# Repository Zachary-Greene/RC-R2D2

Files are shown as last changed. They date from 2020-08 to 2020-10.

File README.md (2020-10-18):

# Mini Remote Control R2D2

This repo is for my mini remote control R2D2 project. It includes all the stl files, all the code files, and the f3z (Fusion 360) file. It also includes some Fusion 360 renders and some extra images.

## Prerequisites
All you need is access to a 3D printer, some skills with through-hole soldering and the parts needed.

## Assembly
First solder the components on to the PCB, making sure that they are the right way around and aligned with the silkscreen. Then place the main PCB in the bottom of the body. Place the motors in the mounts in the feet and push the wires through the feet and legs. Then push and glue if necessary the foot to the corresponding leg, eg left foot to left leg. Then push the legs through the holes in the body, making sure to get the in the right orientation, then push the fastening bolt through the holes to secure the legs in the correct position, then glue them. Repeat for the other leg. For the center foot, put the axle through the wheel and glue the axle in place, not the wheel. For the head mechanism, put the motor inside the head stem with the motor lock glued in place under it, then slide the head stem on to the pegs pointing upwards from the body, from there, put the head on to the head stem with some glue. You then plug the wires into the main PCB, turn it on and put the head on top. For the controller, solder the components on and enjoy. (The wheels are lego wheels as they are what I have handy from siblings and will probably be changed in the coming time.)

## Programming
Plug the ATmega328P into a programmer and burn the bootloader if it doesnt already have one. Then upload the corresponding sketch and put the IC in the proper socket.

## Parts
### Main PCB
* ATmega328P Digikey x1
* LD1117V33 (COM-00526) Sparkfun/Core Electronics x1
* NRF24L01 x1
* NPN Transistor (COM-00521) Sparkfun/Core Electronics x12
* 4xAA Battery Holder (PRT-12083) Sparkfun/Core Electronics x1
#### The following is for an optional speaker system
* 0.1uF Ceramic Capacitor (COM-08375) Sparkfun/Core Electronics x1
* 1.25K Ohm Resistor Digikey x1
* 8 Ohm Speaker x1
* DFPlayer Mini (DFR0299) Core Electronics x1

### Controller PCB
* ATmega328P Digikey x1
* LD1117V33 (COM-00526) Sparkfun/Core Electronics x1
* Thumb Joystick (COM-09032) Sparkfun/Core Electronics x2
* NRF24L01 x1
* 4xAA Battery Holder (PRT-12083) Sparkfun/Core Electronics x1

## Renders
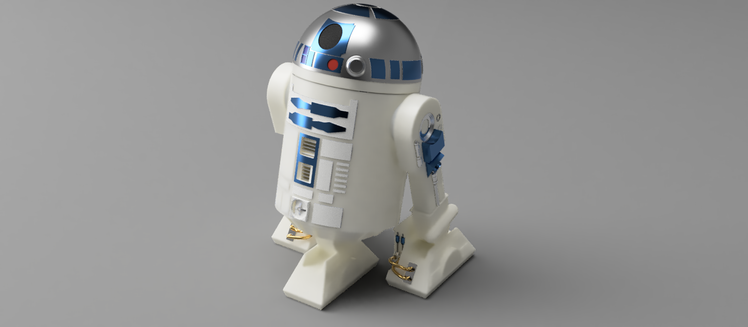
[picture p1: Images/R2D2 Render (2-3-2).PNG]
R2D2 2-3-2 Configuration

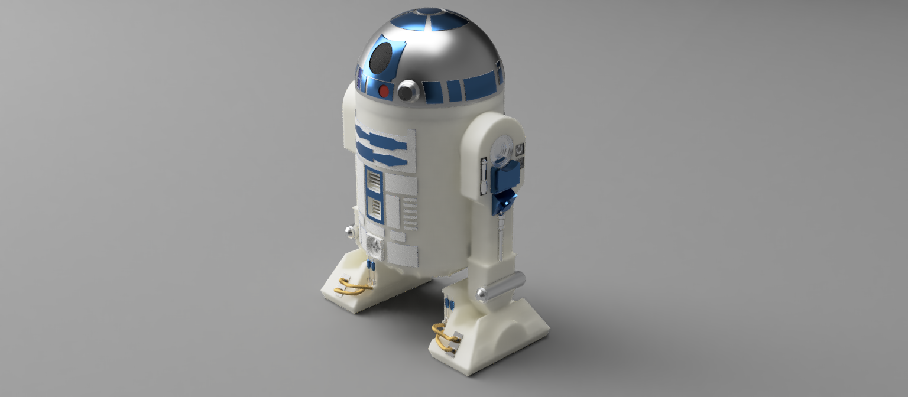
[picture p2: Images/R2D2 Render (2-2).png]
R2D2 2-2 Configuration


## License
See LICENSE.md

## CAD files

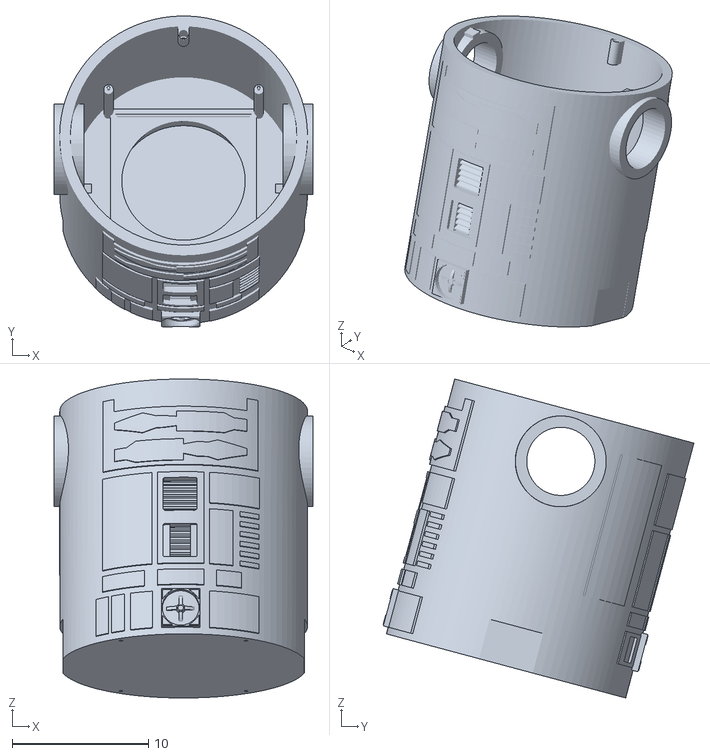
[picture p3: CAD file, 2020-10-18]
STL/Body/Body.stl
19.0 x 22.8 x 23.4

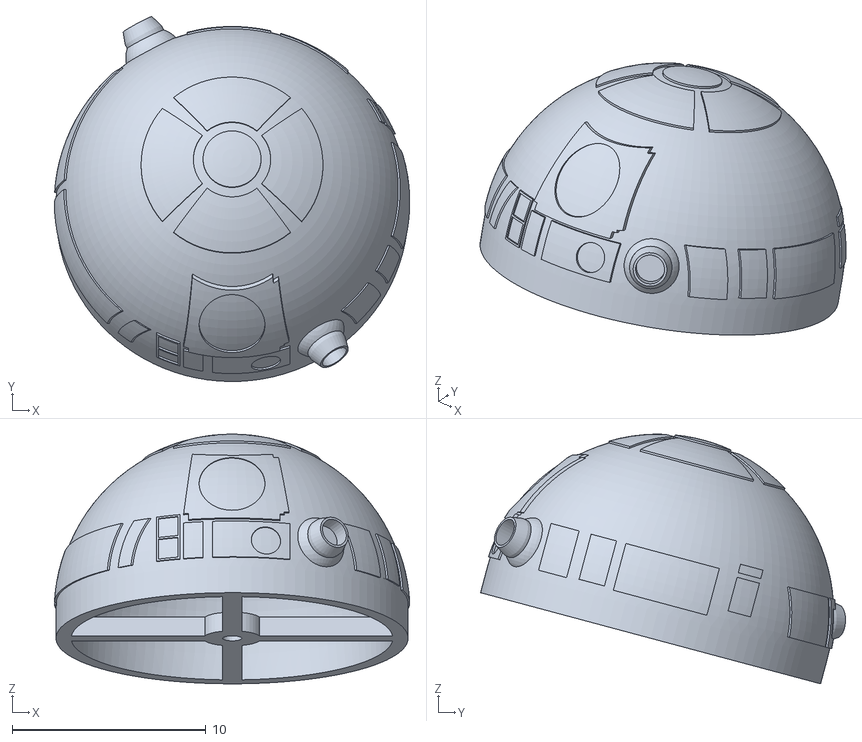
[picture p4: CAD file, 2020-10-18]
STL/Head/Head.stl
18.4 x 18.9 x 12.9

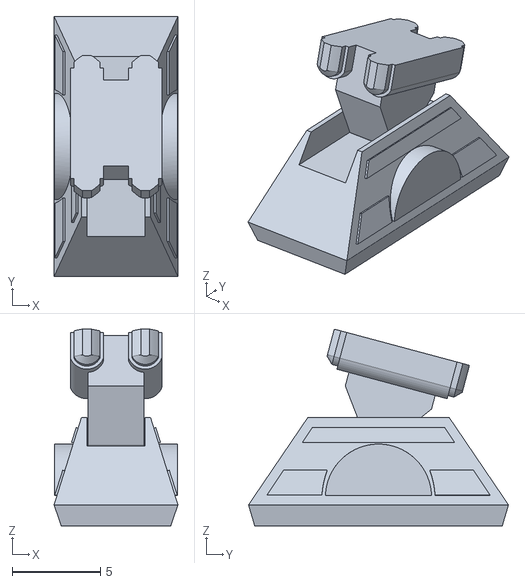
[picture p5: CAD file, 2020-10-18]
STL/Legs/Centre Foot.stl
7.01 x 14.7 x 11.1

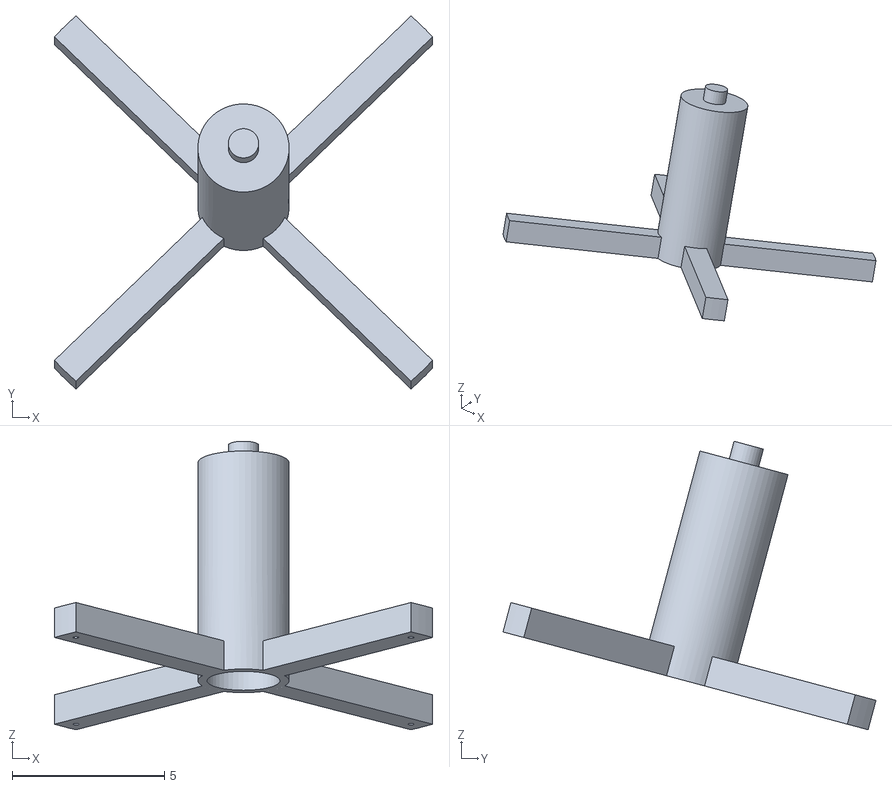
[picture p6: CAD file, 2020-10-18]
STL/Head/Head Stem.stl
12.4 x 12.3 x 9.48

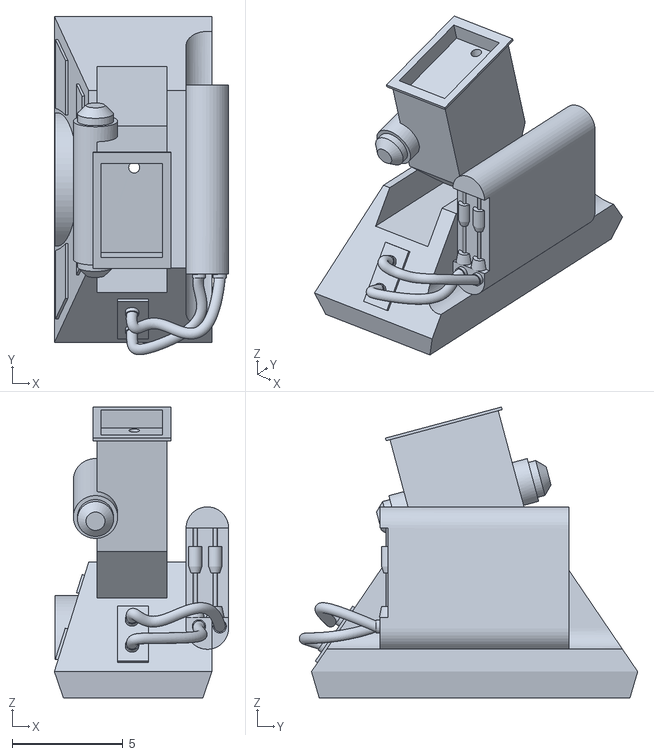
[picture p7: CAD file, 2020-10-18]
STL/Legs/Right Foot.stl
7.85 x 15.3 x 13.1

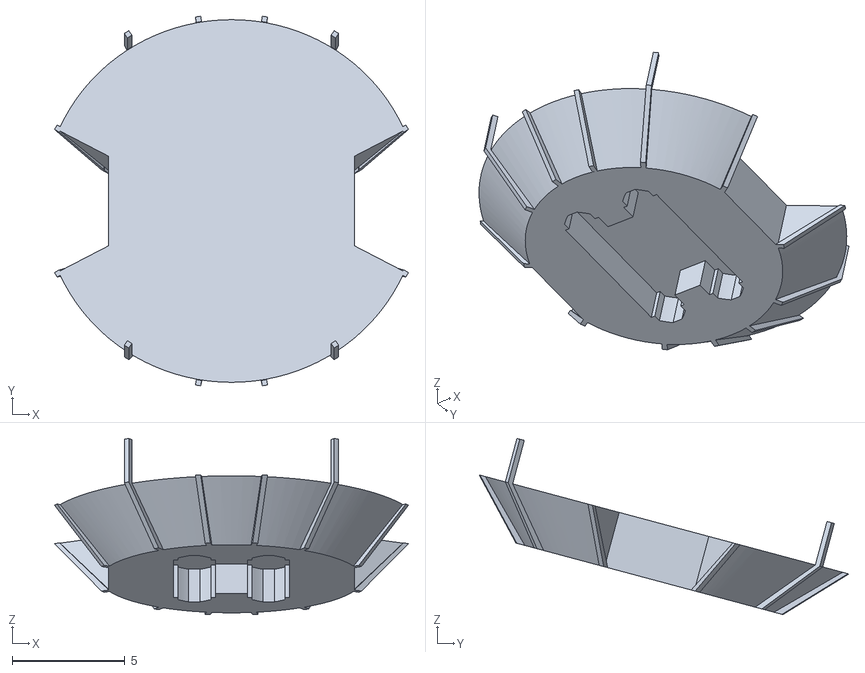
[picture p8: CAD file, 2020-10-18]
STL/Body/Skirt.stl
15.7 x 16.4 x 7.82

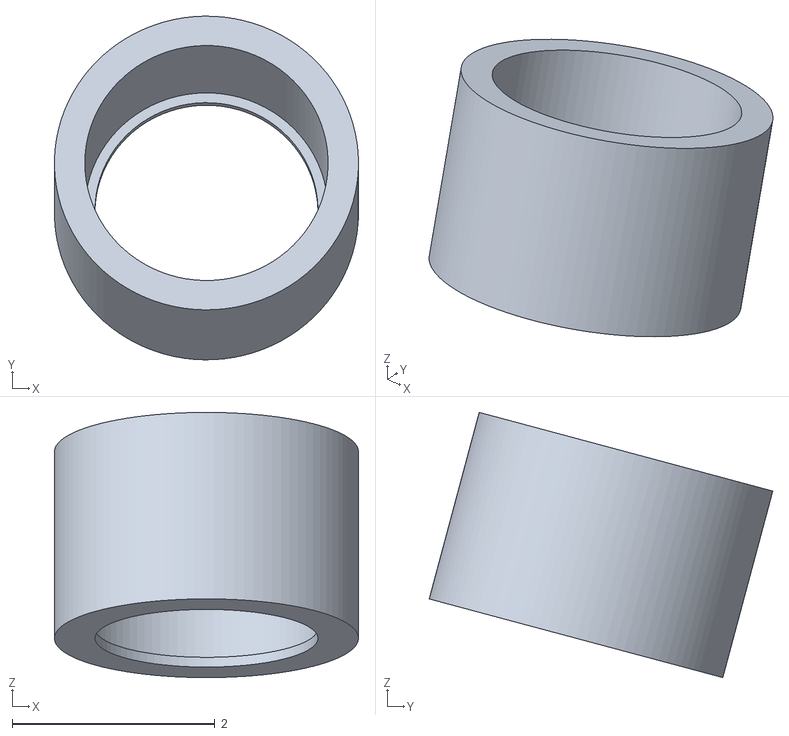
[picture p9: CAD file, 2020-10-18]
STL/Head/Motor Lock.stl
3.00 x 3.39 x 2.62

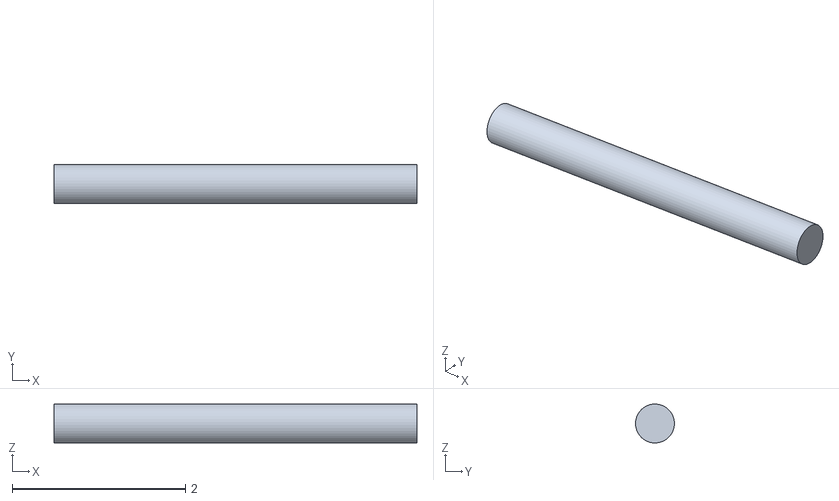
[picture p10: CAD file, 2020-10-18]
STL/Legs/Center Axle.stl
4.19 x 0.449 x 0.45

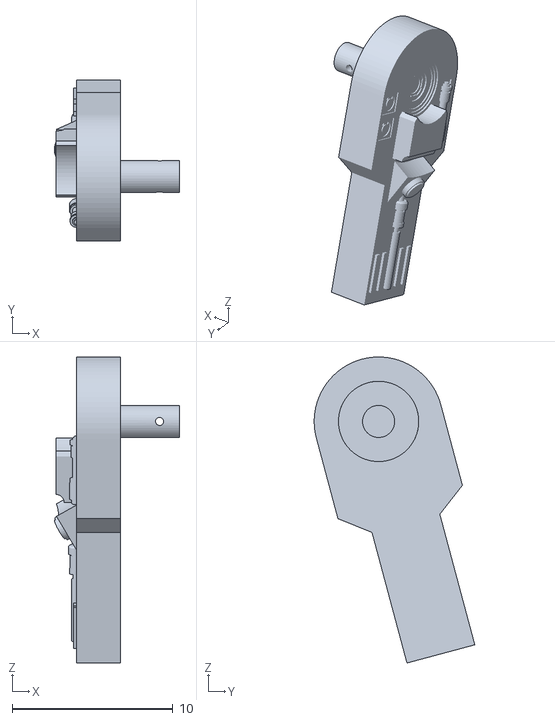
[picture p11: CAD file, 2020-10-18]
STL/Legs/Right Leg.stl
7.80 x 10.0 x 19.1

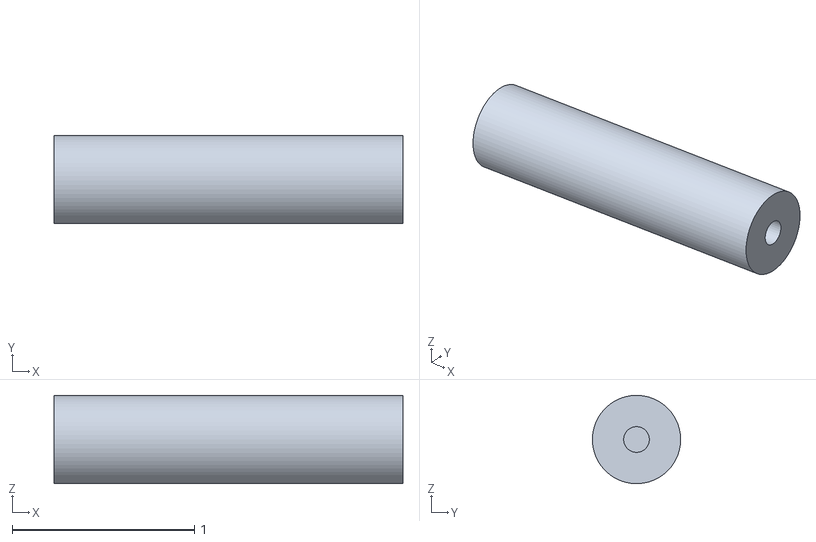
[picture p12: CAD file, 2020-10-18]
STL/Legs/Wheel Adapter (Print 2).stl
1.92 x 0.485 x 0.485

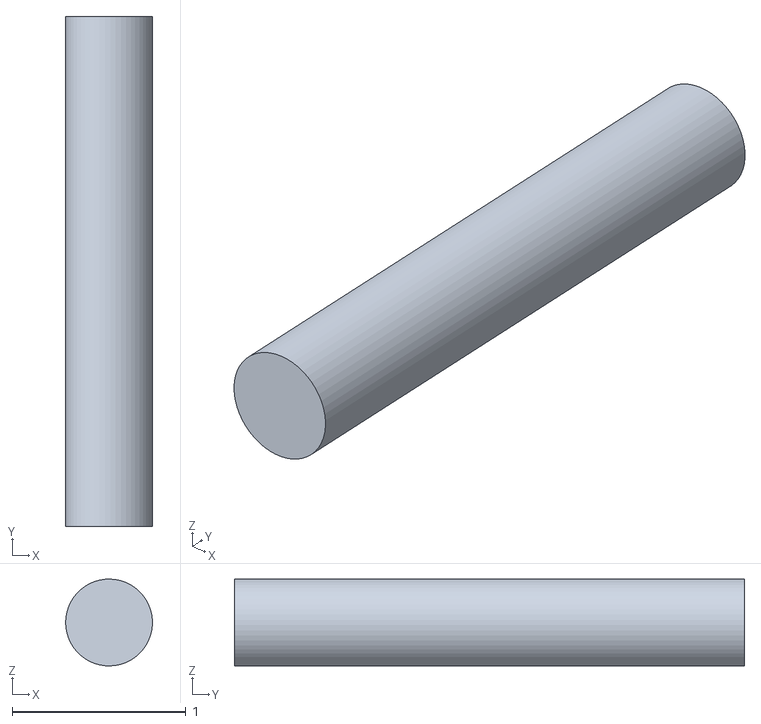
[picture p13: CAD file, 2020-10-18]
STL/Body/Fastening Bolt (Print 2).stl
0.5 x 2.93 x 0.5

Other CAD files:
STL/Legs/Left Leg.stl
STL/Legs/Left Foot.stl

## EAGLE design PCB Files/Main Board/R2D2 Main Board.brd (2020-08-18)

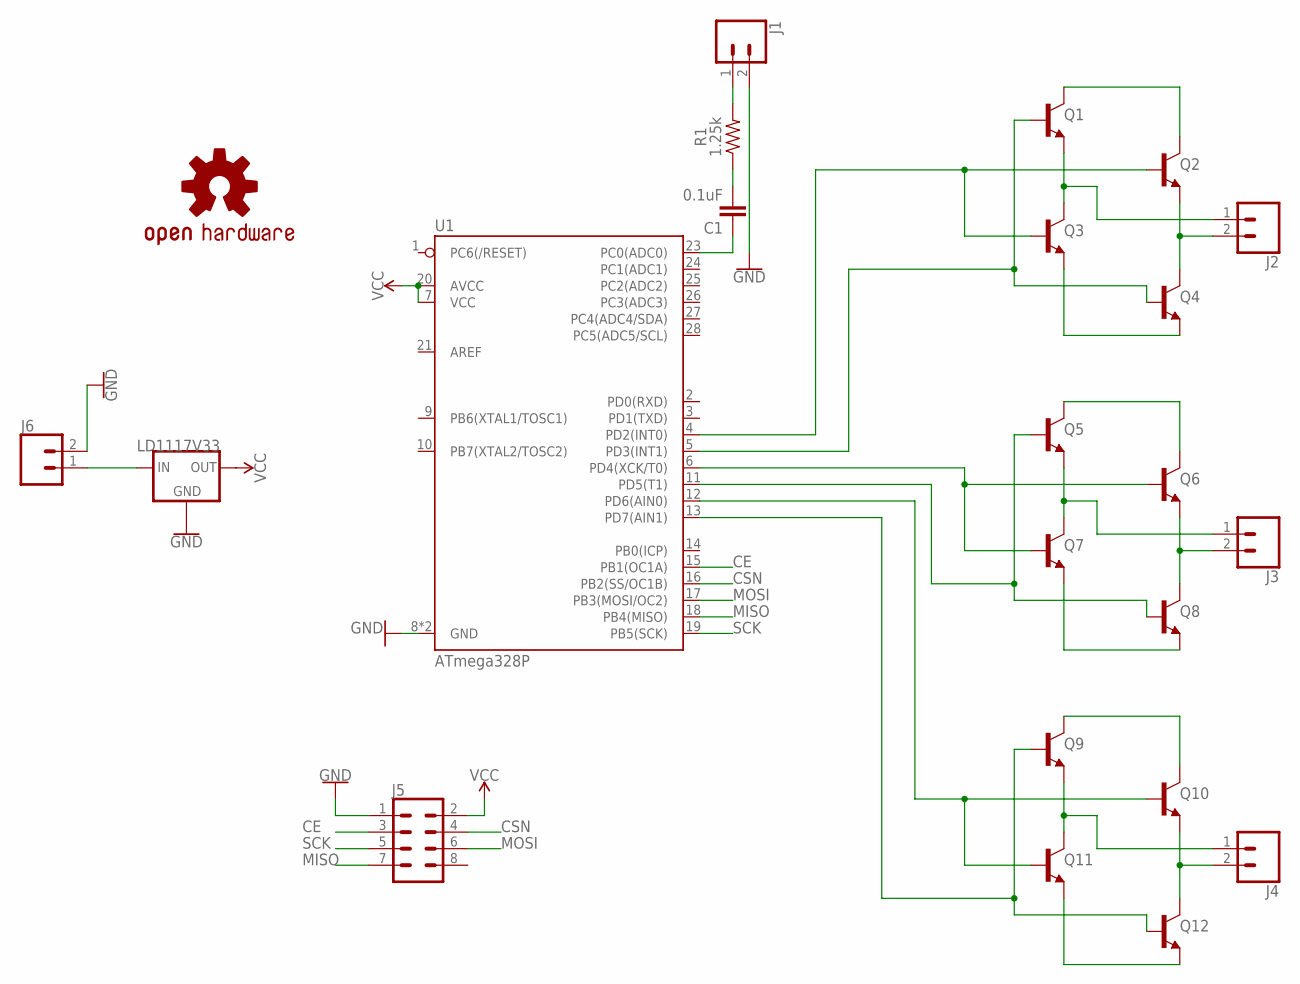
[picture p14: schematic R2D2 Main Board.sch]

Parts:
C1: 0.1uF; CAP-PTH-SMALL-KIT
J1, J2, J3, J4, J6: CONN_02; 1X02
J5: CONN_04X2; 2X4
LOGO1: OSHW-LOGOL; OSHW-LOGO-L
Q1, Q2, Q3, Q4, Q5, Q6, Q7, Q8, Q9, Q10, Q11, Q12: 200mA/40V; TO-92
R1: 1.25k; AXIAL-0.3
U1: ATmega328P; DIP28
U$1: LD1117V33; 78XXL

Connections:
CE: J5.3, U1.15 (PB1(OC1A))
CSN: J5.4, U1.16 (PB2(SS/OC1B))
GND: J1.2, J5.1, J6.2, U1.8 (GND), U1.22 (GND), U$1.IN (GND)
MISO: J5.7, U1.18 (PB4(MISO))
MOSI: J5.6, U1.17 (PB3(MOSI/OC2))
unnamed: Q1.3 (C), Q2.3 (C)
unnamed: Q3.1 (E), Q4.1 (E)
unnamed: J2.2, Q2.1 (E), Q4.3 (C)
unnamed: J2.1, Q1.1 (E), Q3.3 (C)
unnamed: Q2.2 (B), Q3.2 (B), U1.4 (PD2(INT0))
unnamed: Q1.2 (B), Q4.2 (B), U1.5 (PD3(INT1))
unnamed: Q5.3 (C), Q6.3 (C)
unnamed: Q7.1 (E), Q8.1 (E)
unnamed: J3.2, Q6.1 (E), Q8.3 (C)
unnamed: J3.1, Q5.1 (E), Q7.3 (C)
unnamed: Q6.2 (B), Q7.2 (B), U1.6 (PD4(XCK/T0))
unnamed: Q5.2 (B), Q8.2 (B), U1.11 (PD5(T1))
unnamed: Q9.3 (C), Q10.3 (C)
unnamed: Q11.1 (E), Q12.1 (E)
unnamed: J4.2, Q10.1 (E), Q12.3 (C)
unnamed: J4.1, Q9.1 (E), Q11.3 (C)
unnamed: Q10.2 (B), Q11.2 (B), U1.12 (PD6(AIN0))
unnamed: Q9.2 (B), Q12.2 (B), U1.13 (PD7(AIN1))
unnamed: C1.1, U1.23 (PC0(ADC0))
unnamed: C1.2, R1.P$1 (1)
unnamed: J1.1, R1.P$2 (2)
SCK: J5.5, U1.19 (PB5(SCK))
VCC: J5.2, U1.7 (VCC), U1.20 (AVCC), U$1.GND (OUT)
VIN: J6.1, U$1.OUT (IN)

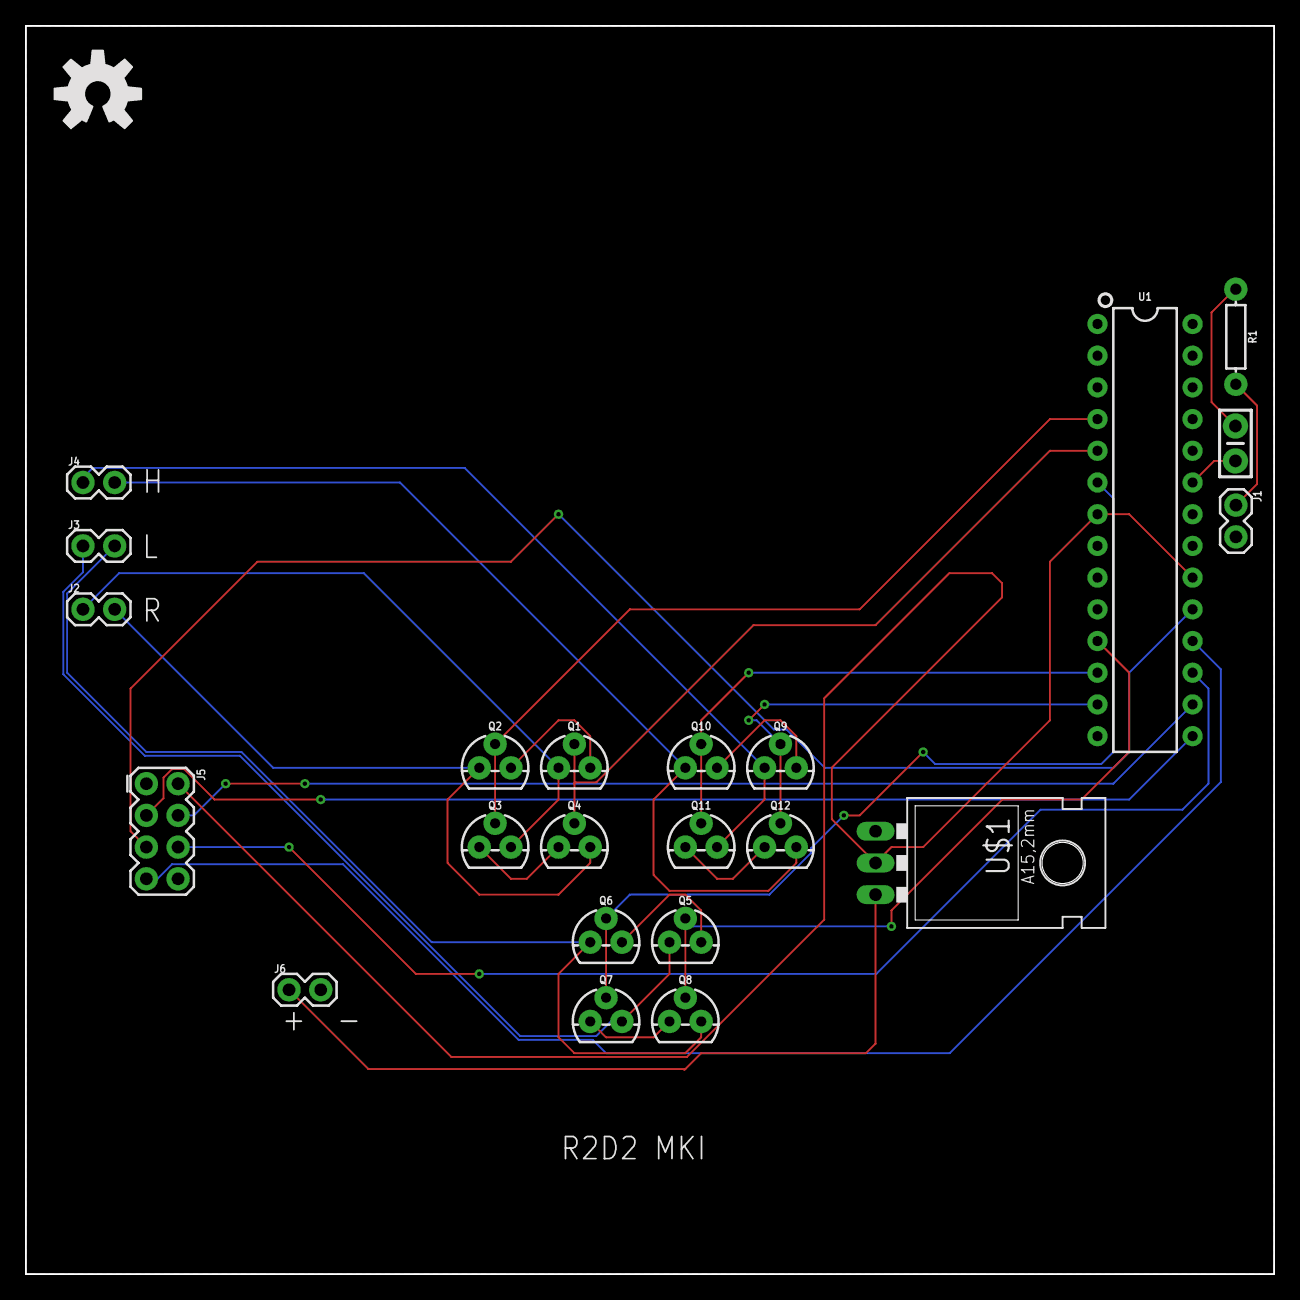
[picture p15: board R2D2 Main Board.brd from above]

Board: 2 copper layers, 100.0 x 100.0 mm, 23 parts (0 on the bottom side), 29 nets.

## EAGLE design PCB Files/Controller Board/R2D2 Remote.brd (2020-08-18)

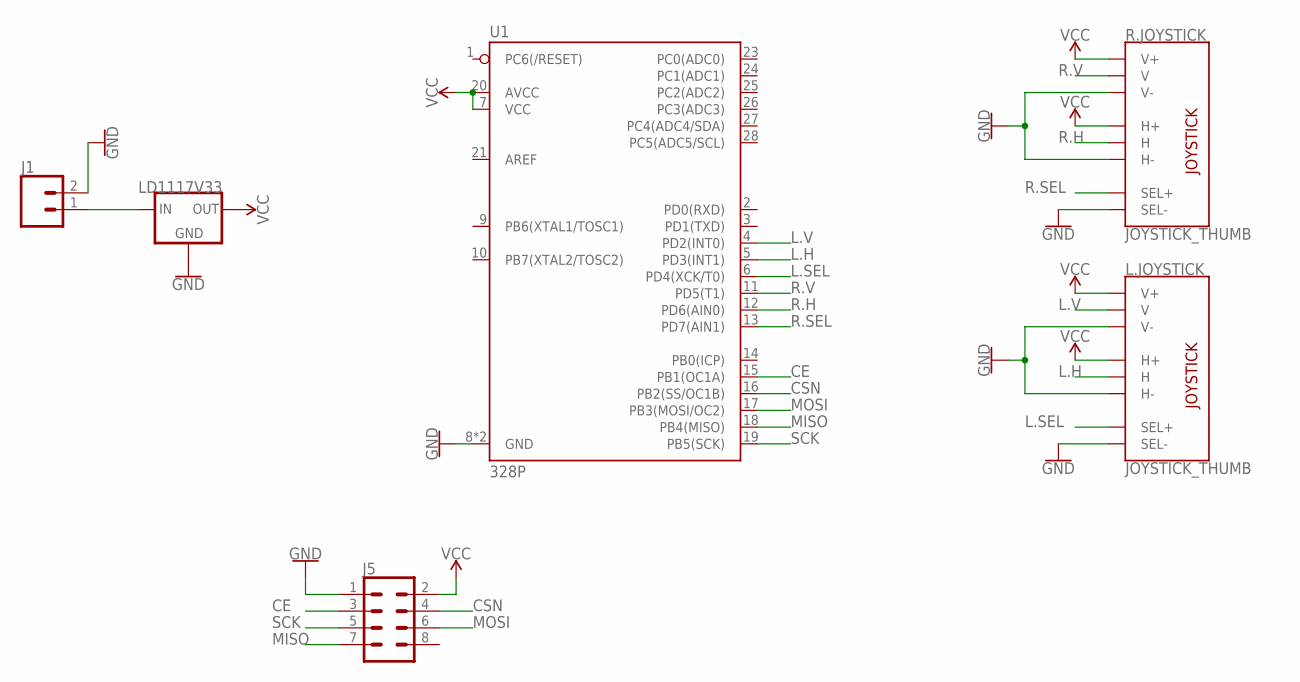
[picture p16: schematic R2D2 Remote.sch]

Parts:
J1: CONN_02; 1X02
J5: CONN_04X2; 2X4
L.JOYSTICK: JOYSTICK_THUMB; JOYSTICK
R.JOYSTICK: JOYSTICK_THUMB; JOYSTICK
U1: 328P; DIP28
U$1: LD1117V33; 78XXL

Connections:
CE: J5.3, U1.15 (PB1(OC1A))
CSN: J5.4, U1.16 (PB2(SS/OC1B))
GND: J1.2, J5.1, L.JOYSTICK.B2A (SEL-), L.JOYSTICK.H3 (H-), L.JOYSTICK.V3 (V-), R.JOYSTICK.B2A (SEL-), R.JOYSTICK.H3 (H-), R.JOYSTICK.V3 (V-), U1.8 (GND), U1.22 (GND), U$1.IN (GND)
L.H: L.JOYSTICK.H2 (H), U1.5 (PD3(INT1))
L.SEL: L.JOYSTICK.B1A (SEL+), U1.6 (PD4(XCK/T0))
L.V: L.JOYSTICK.V2 (V), U1.4 (PD2(INT0))
MISO: J5.7, U1.18 (PB4(MISO))
MOSI: J5.6, U1.17 (PB3(MOSI/OC2))
unnamed: J1.1, U$1.OUT (IN)
R.H: R.JOYSTICK.H2 (H), U1.12 (PD6(AIN0))
R.SEL: R.JOYSTICK.B1A (SEL+), U1.13 (PD7(AIN1))
R.V: R.JOYSTICK.V2 (V), U1.11 (PD5(T1))
SCK: J5.5, U1.19 (PB5(SCK))
VCC: J5.2, L.JOYSTICK.H1 (H+), L.JOYSTICK.V1 (V+), R.JOYSTICK.H1 (H+), R.JOYSTICK.V1 (V+), U1.7 (VCC), U1.20 (AVCC), U$1.GND (OUT)

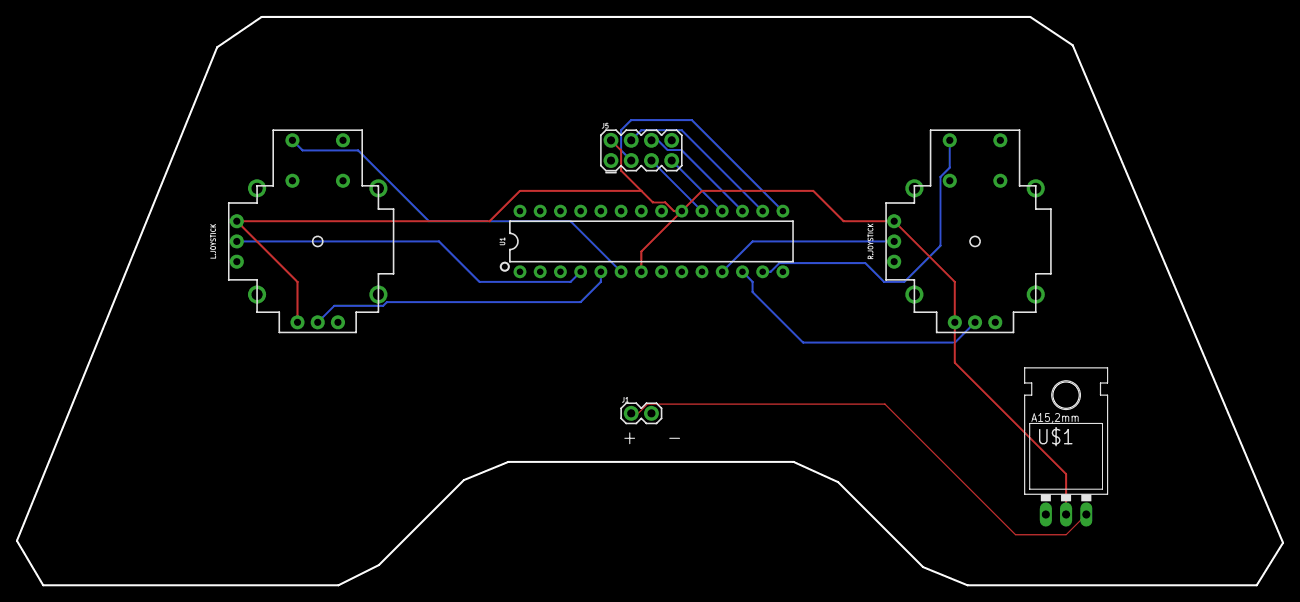
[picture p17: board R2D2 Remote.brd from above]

Board: 2 copper layers, 159.0 x 71.4 mm, 6 parts (0 on the bottom side), 14 nets.

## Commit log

2020-08-18 Added PCB files for main and controller
    [R2D2 Main Board.brd, R2D2 Main Board.sch, R2D2 Remote.brd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]
2020-10-18 Created STL folder
2020-10-18 Add files via upload
    Added all STL files
    [Body.stl, Center Axle.stl, Centre Foot.stl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]

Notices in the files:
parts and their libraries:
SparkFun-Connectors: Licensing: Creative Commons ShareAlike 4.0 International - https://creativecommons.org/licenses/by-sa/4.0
